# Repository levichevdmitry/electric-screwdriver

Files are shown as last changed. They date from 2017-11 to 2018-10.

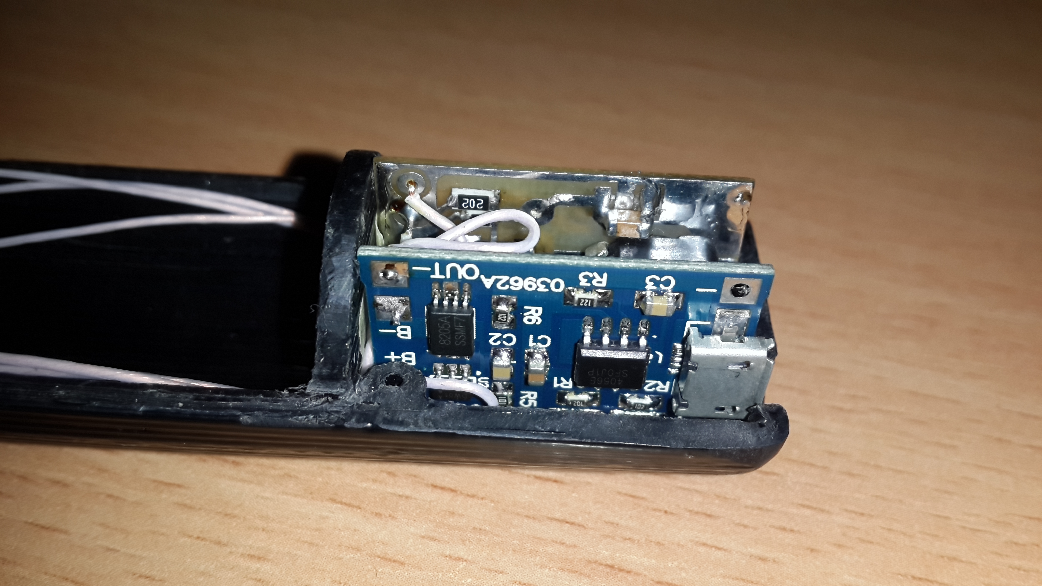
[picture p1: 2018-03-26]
foto/20171118_213815.jpg

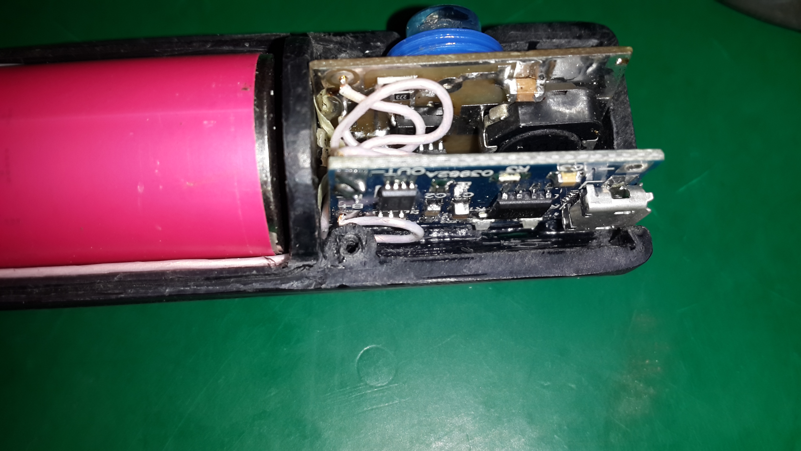
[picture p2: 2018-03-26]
foto/20180302_205503.jpg

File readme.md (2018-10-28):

Электроотвертка
-------------------------------
**Структура проекта**
- src - папка содержит исходные коды и прошивку для контроллера отвертки
- hardware - папка содержит файлы схем и печатных плат
- models - папка содержить модели корпуса и кнопок
- foto - папка содержит фото готового устройства и  этапов сборки

**Инструкция по сборке**

Смотрите статью на habr.ru
https://habr.com/post/411203/

Модели для печати лежат вот тут https://www.thingiverse.com/thing:2746308

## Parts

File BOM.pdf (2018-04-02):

Перечень элементов для сборки электроотвертки

№ | Наименование | Фото | Количество
Элементы механики

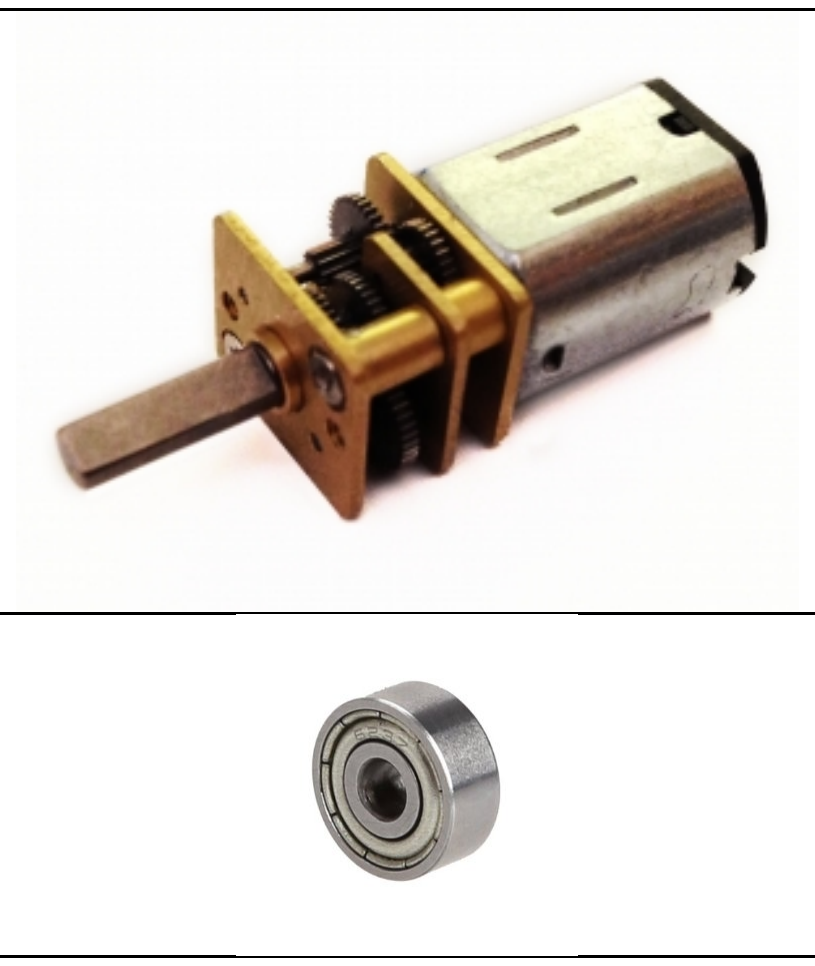
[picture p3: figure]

1. Мотор c редуктором 6В 250 об/мин | ZGRM12FT20-250 | 1
2. | Подшипник закрытый 623zz | 1
3. Муфта соединительная латунная, | внутренний диаметр 3 мм. | 1
4. | Винт стопорный 4мм х М3 | 2
5. Корпус пластиковый из 2 частей + | толкатели кнопок. Материал ABS. 3D печать. Масса используемого филамента примерно 40 г. | 1

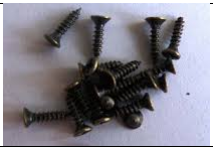
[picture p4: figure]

6. | Саморезы для сборки корпуса 2.5х6 мм | 6
7. Полоска латуни 5х15мм толщиной 0.5 мм | для контактов аккумулятора. | 2
8. | Удлинитель из набора с битами 4 мм | 1

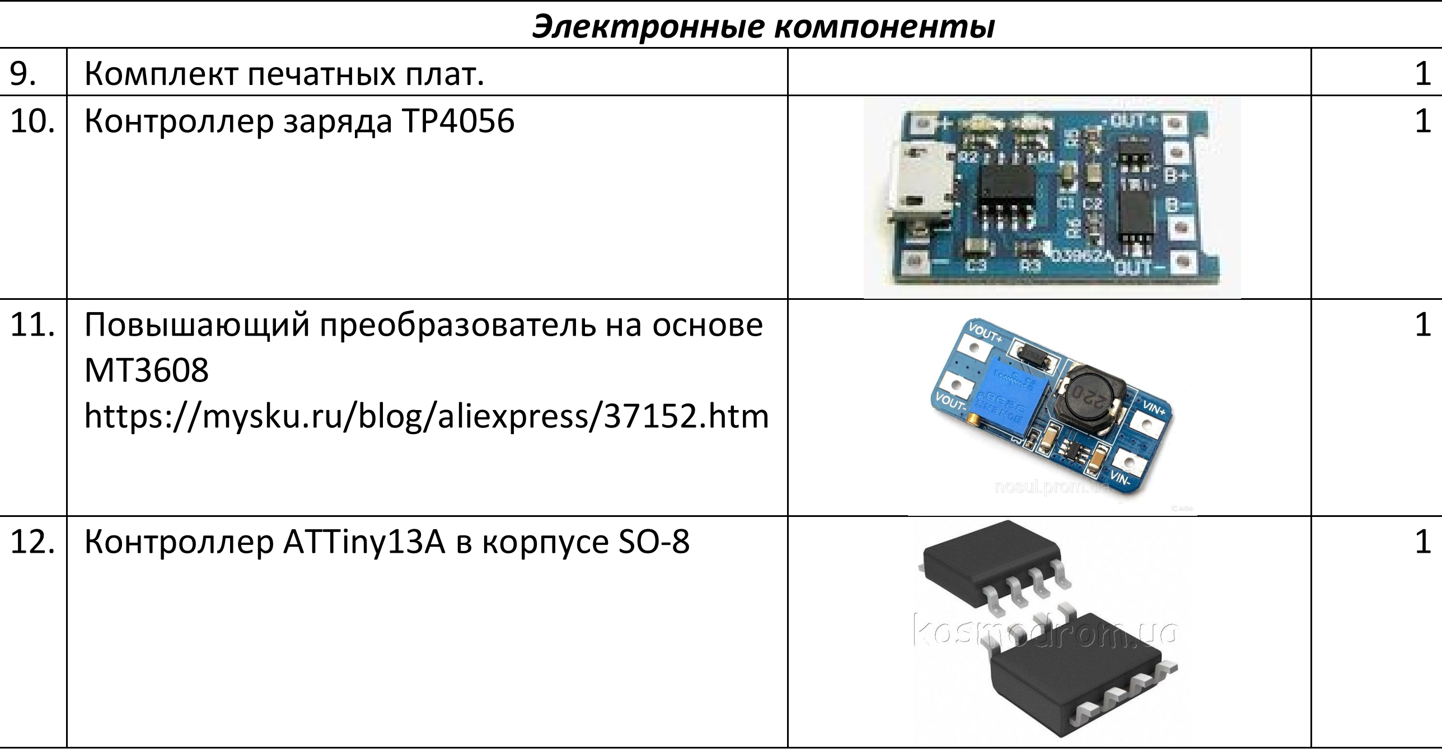
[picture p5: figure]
Электронные компоненты; Комплект печатных плат.; Контроллер заряда TP4056

11. Повышающий преобразователь на основе | MT3608 https://mysku.ru/blog/aliexpress/37152.htm | 1
12. | Контроллер ATTiny13A в корпусе SO-8 | 1

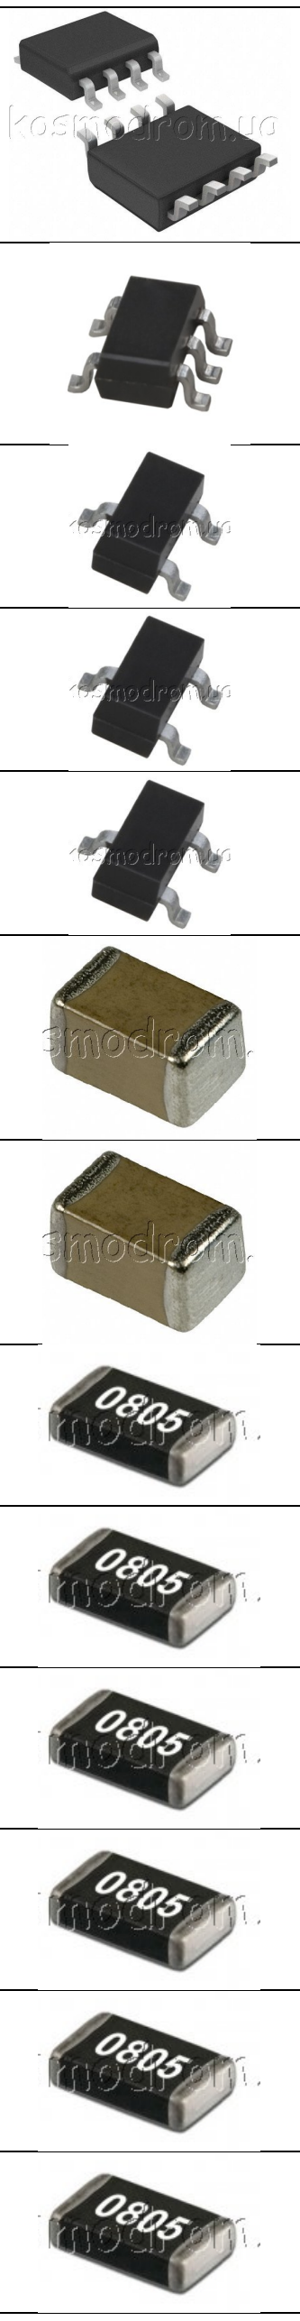
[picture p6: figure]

13. | Драйвер MX612 | 1
14. Стабилизатор 3.0В LP2981-30 в корпусе | SOT-23-5 | 1
15. | Транзистор BC817 | 2
16. | Транзистор BC857 | 1
17. | Транзистор IRLML6402 P-chanel | 1
18. | 100n 0805 | 7
19. | 1u 0805 | 1
20. | 100k 0805 | 2
21. | 27k 0805 | 1
22. | 20k 0805 | 3
23. | 10k 0805 | 6
24. | 4.7k 0805 | 2
25. | 2.7k 0805 | 1

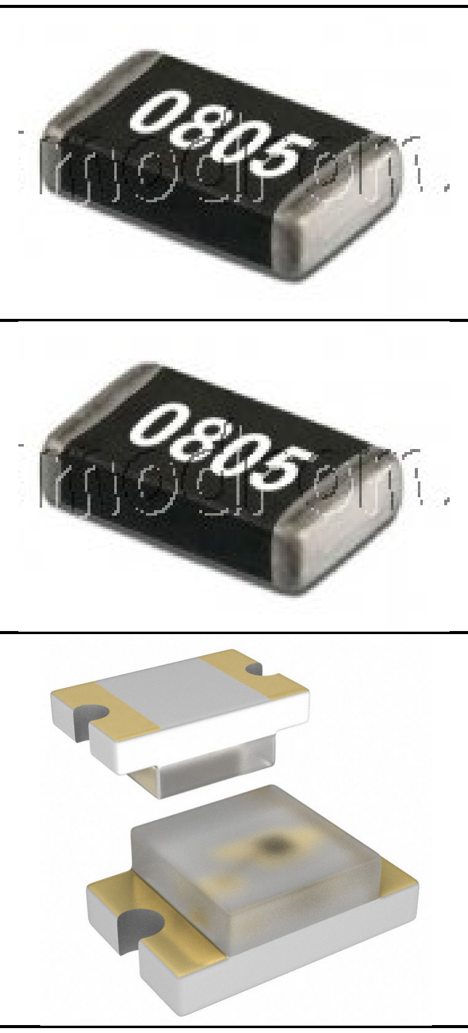
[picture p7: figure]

26. | 2k 0805 | 1
27. | 220 Om 0805 | 1
28. | Led Red 0805 | 1
29. | Провод МГТФ 0.35 мм | 0.5 м

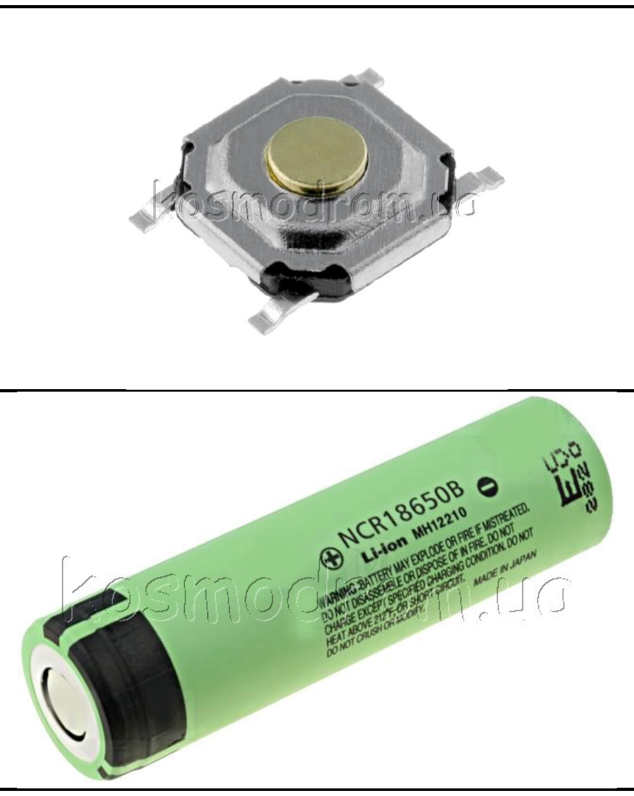
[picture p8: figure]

30. Кнопка тактовая | TACTB-64K-F | 4
31. | Аккумулятор типоразмера 18650 | 1

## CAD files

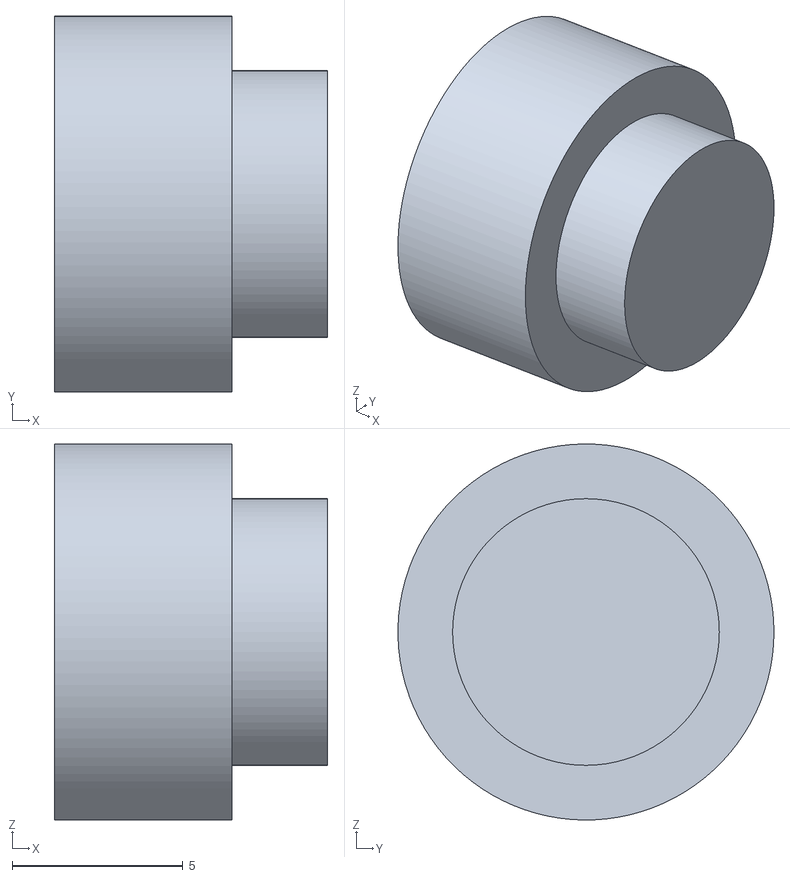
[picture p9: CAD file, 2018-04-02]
models/pwr_btn.stl
8.00 x 11.0 x 11.0

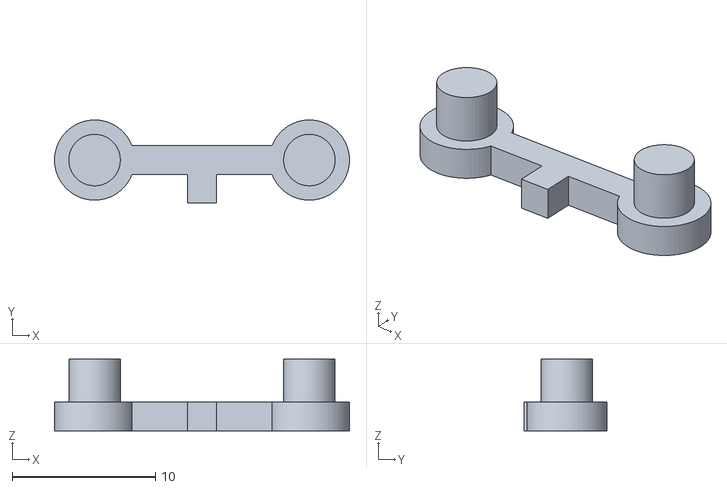
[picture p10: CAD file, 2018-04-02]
models/fwd_rev_btns.stl
20.6 x 5.80 x 5.00

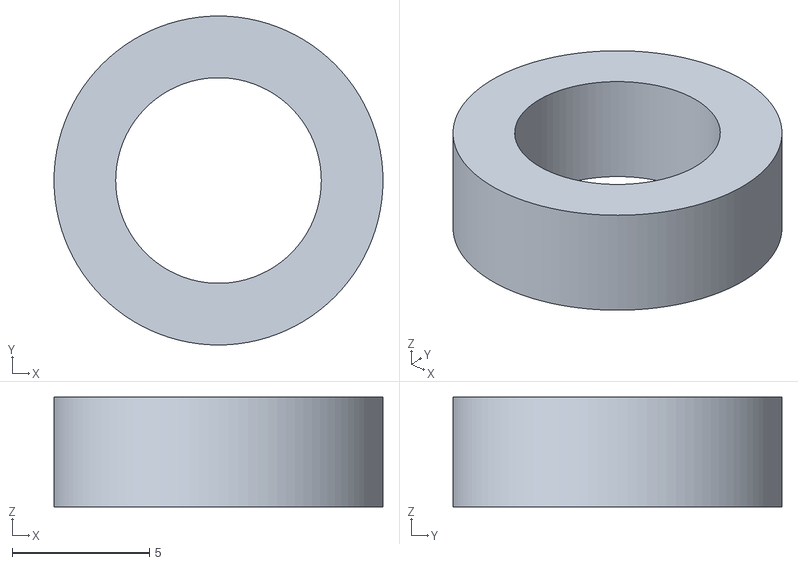
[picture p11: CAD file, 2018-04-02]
models/pwr_btn_ring.stl
12.0 x 12.0 x 4.00

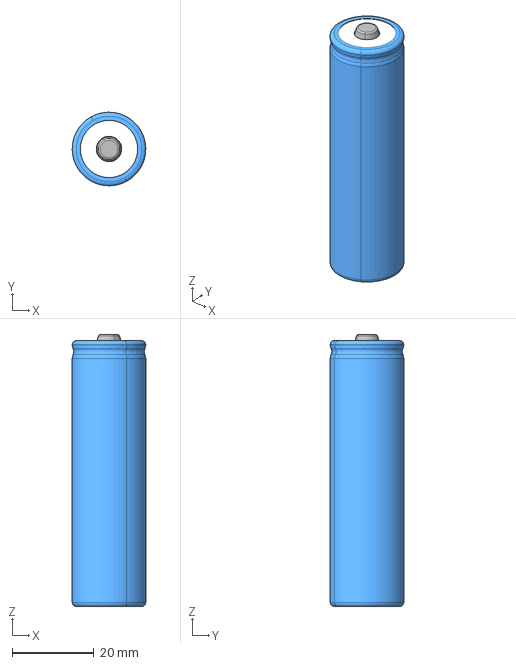
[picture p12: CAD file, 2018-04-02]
models/Battery 18650.igs
18.0 x 18.0 x 66.5 mm

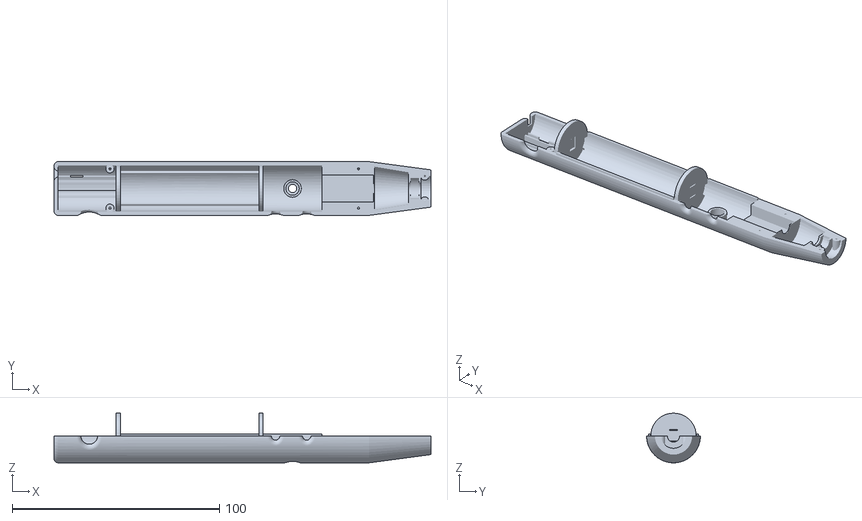
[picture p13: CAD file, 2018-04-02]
models/korpus_1.stl
182.0 x 26.0 x 24.0

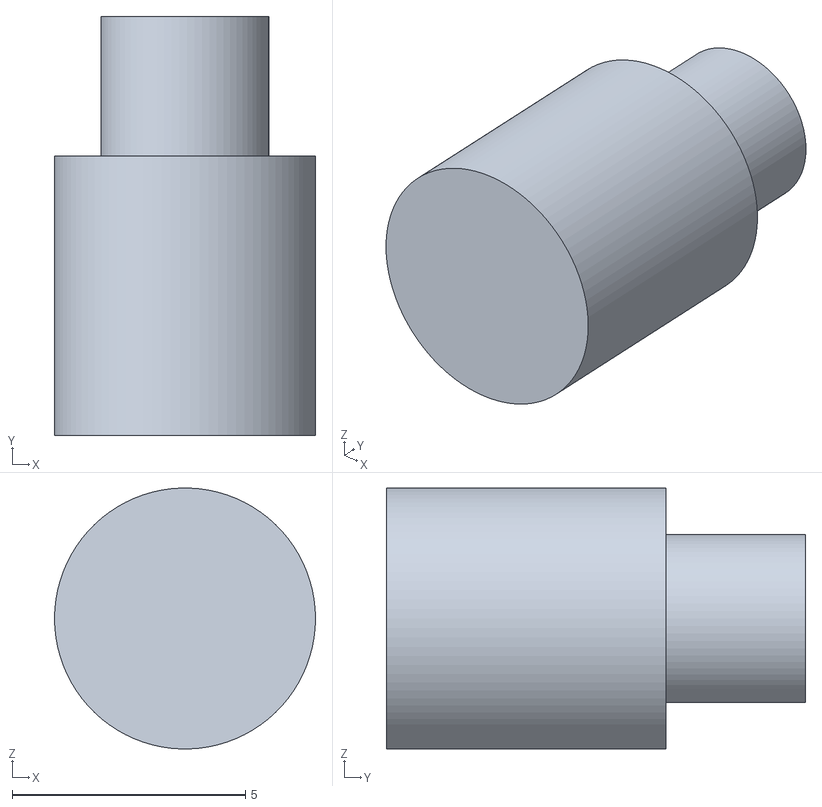
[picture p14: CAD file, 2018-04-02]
models/btn.stl
5.60 x 9.00 x 5.60

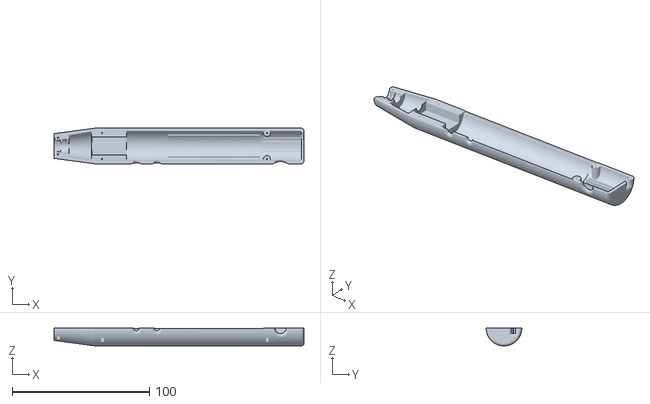
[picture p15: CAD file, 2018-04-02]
models/korpus_2.stl
182.0 x 26.0 x 13.0

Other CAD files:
models/623zz/OldVersions/roulement_623-2z_0.0001.iam
models/623zz/OldVersions/roulement_623-2z_0_01.0001.ipt
models/623zz/OldVersions/roulement_623-2z_0_02.0001.ipt
models/623zz/OldVersions/roulement_623-2z_0_03.0001.ipt
models/623zz/OldVersions/roulement_623-2z_0_04.0001.ipt
models/623zz/OldVersions/roulement_623-2z_0_05.0001.ipt
models/623zz/roulement_623-2z_0.iam
models/623zz/roulement_623-2z_0_01.ipt
models/623zz/roulement_623-2z_0_02.ipt
models/623zz/roulement_623-2z_0_03.ipt
models/623zz/roulement_623-2z_0_04.ipt
models/623zz/roulement_623-2z_0_05.ipt
models/Bateria 18650.ipt
models/Battery 18650.ipt
models/OldVersions/Vtulka.0001.ipt
models/OldVersions/btn.0002.ipt
models/OldVersions/fwd_rev_btns.0002.ipt
models/OldVersions/korpus_1.0021.ipt
models/OldVersions/korpus_2.0006.ipt
models/OldVersions/pwr_btn.0002.ipt
models/OldVersions/Сборка.0015.iam
models/TP4056.ipt
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

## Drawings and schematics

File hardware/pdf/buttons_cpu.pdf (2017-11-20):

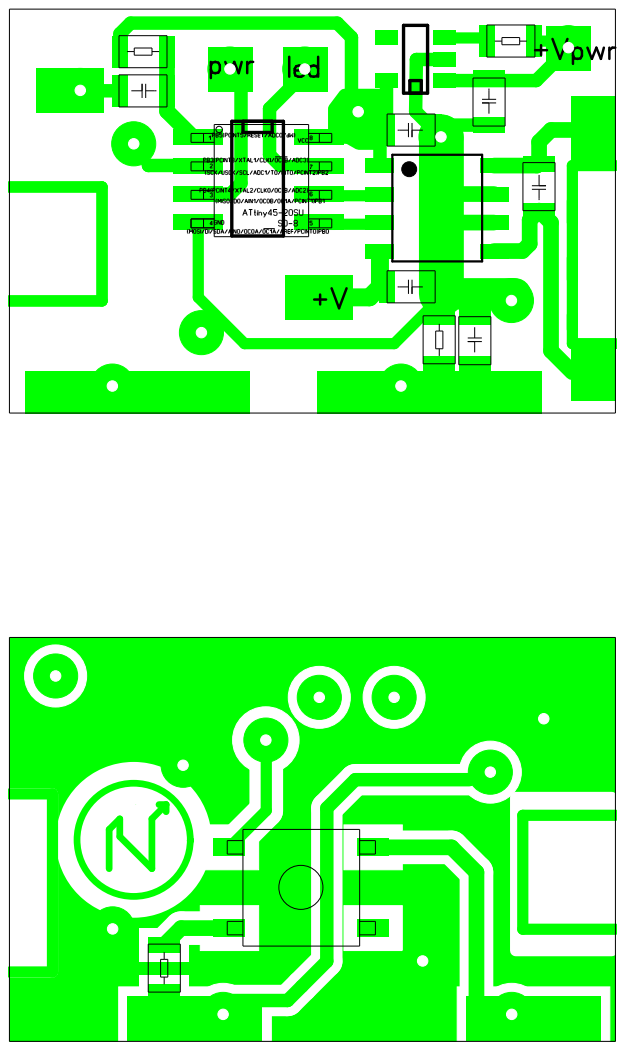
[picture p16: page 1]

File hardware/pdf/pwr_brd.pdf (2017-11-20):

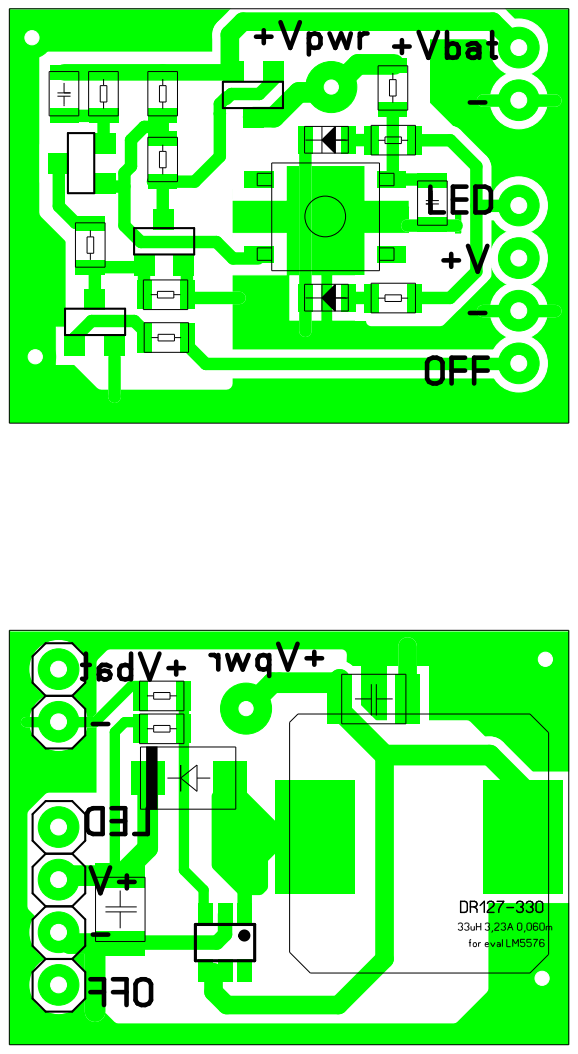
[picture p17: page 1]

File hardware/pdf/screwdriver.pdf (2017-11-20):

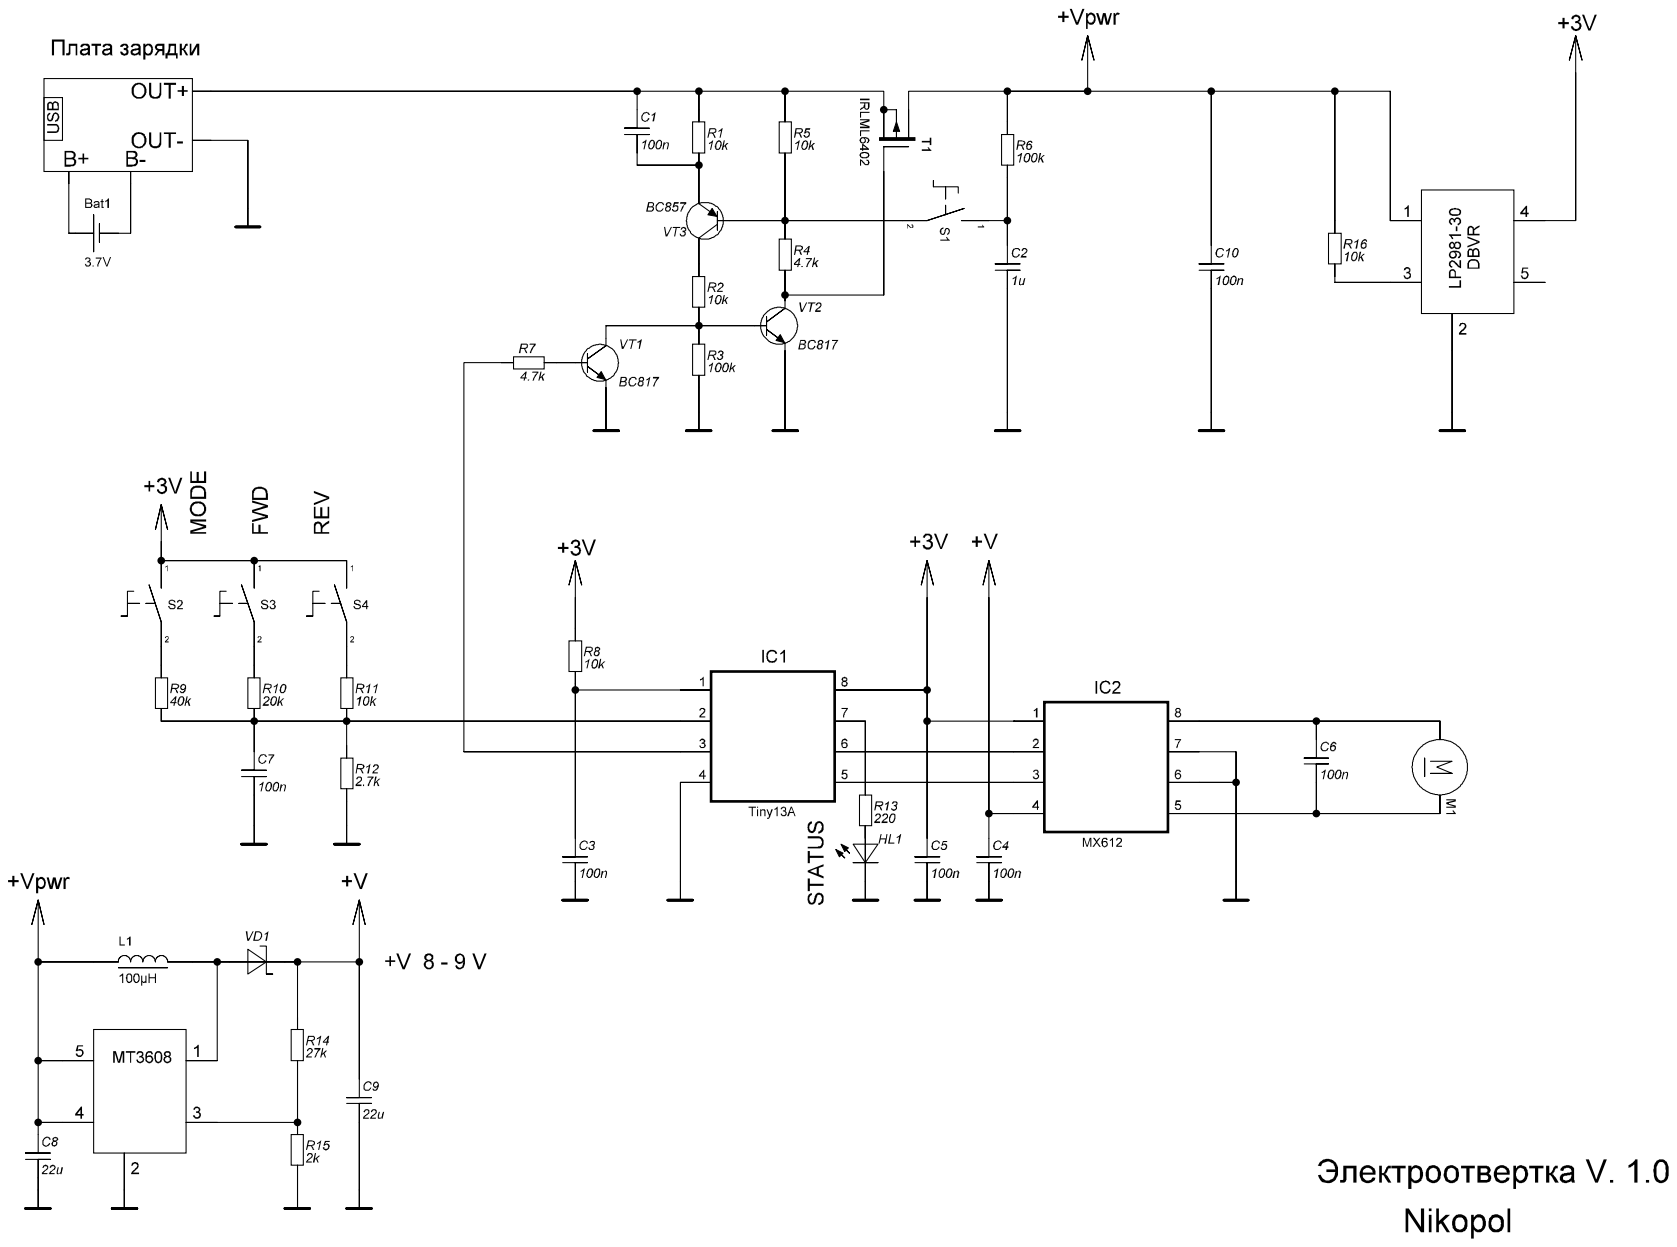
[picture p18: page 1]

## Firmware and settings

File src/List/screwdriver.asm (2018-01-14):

;CodeVisionAVR C Compiler V2.05.3 Standard
;(C) Copyright 1998-2011 Pavel Haiduc, HP InfoTech s.r.l.
;http://www.hpinfotech.com

;Chip type                : ATtiny13A
;Program type             : Application
;Clock frequency          : 9,600000 MHz
;Memory model             : Tiny
;Optimize for             : Size
;(s)printf features       : int, width
;(s)scanf features        : int, width
;External RAM size        : 0
;Data Stack size          : 16 byte(s)
;Heap size                : 0 byte(s)
;Promote 'char' to 'int'  : Yes
;'char' is unsigned       : Yes
;8 bit enums              : Yes
;Global 'const' stored in FLASH     : No
;Enhanced function parameter passing: Yes
;Smart register allocation          : Off
;Automatic register allocation      : On

	#pragma AVRPART ADMIN PART_NAME ATtiny13A
	#pragma AVRPART MEMORY PROG_FLASH 1024
	#pragma AVRPART MEMORY EEPROM 64
	#pragma AVRPART MEMORY INT_SRAM SIZE 159
	#pragma AVRPART MEMORY INT_SRAM START_ADDR 0x60

	.LISTMAC
	.EQU EERE=0x0
	.EQU EEWE=0x1
	.EQU EEMWE=0x2
	.EQU EECR=0x1C
	.EQU EEDR=0x1D
	.EQU EEARL=0x1E

	.EQU WDTCR=0x21
	.EQU MCUSR=0x34
	.EQU MCUCR=0x35
	.EQU SPL=0x3D
	.EQU SREG=0x3F

	.DEF R0X0=R0
	.DEF R0X1=R1
	.DEF R0X2=R2
	.DEF R0X3=R3
	.DEF R0X4=R4
	.DEF R0X5=R5
	.DEF R0X6=R6
	.DEF R0X7=R7
	.DEF R0X8=R8
	.DEF R0X9=R9
	.DEF R0XA=R10
	.DEF R0XB=R11
	.DEF R0XC=R12
	.DEF R0XD=R13
	.DEF R0XE=R14
	.DEF R0XF=R15
	.DEF R0X10=R16
	.DEF R0X11=R17
	.DEF R0X12=R18
	.DEF R0X13=R19
	.DEF R0X14=R20
	.DEF R0X15=R21
	.DEF R0X16=R22
	.DEF R0X17=R23
	.DEF R0X18=R24
	.DEF R0X19=R25
	.DEF R0X1A=R26
	.DEF R0X1B=R27
	.DEF R0X1C=R28
	.DEF R0X1D=R29
	.DEF R0X1E=R30
	.DEF R0X1F=R31

	.EQU __SRAM_START=0x0060
	.EQU __SRAM_END=0x009F
	.EQU __DSTACK_SIZE=0x0010
	.EQU __HEAP_SIZE=0x0000
	.EQU __CLEAR_SRAM_SIZE=__SRAM_END-__SRAM_START+1

	.MACRO __CPD1N
	CPI  R30,LOW(@0)
	LDI  R26,HIGH(@0)
	CPC  R31,R26
	LDI  R26,BYTE3(@0)
	CPC  R22,R26
	LDI  R26,BYTE4(@0)
	CPC  R23,R26
	.ENDM

	.MACRO __CPD2N
	CPI  R26,LOW(@0)
	LDI  R30,HIGH(@0)
	CPC  R27,R30
	LDI  R30,BYTE3(@0)
	CPC  R24,R30
	LDI  R30,BYTE4(@0)
	CPC  R25,R30
	.ENDM

	.MACRO __CPWRR
	CP   R@0,R@2
	CPC  R@1,R@3
	.ENDM

	.MACRO __CPWRN
	CPI  R@0,LOW(@2)
	LDI  R30,HIGH(@2)
	CPC  R@1,R30
	.ENDM

	.MACRO __ADDB1MN
	SUBI R30,LOW(-@0-(@1))
	.ENDM

	.MACRO __ADDB2MN
	SUBI R26,LOW(-@0-(@1))
	.ENDM

	.MACRO __ADDW1MN
	SUBI R30,LOW(-@0-(@1))
	SBCI R31,HIGH(-@0-(@1))
	.ENDM

	.MACRO __ADDW2MN
	SUBI R26,LOW(-@0-(@1))
	SBCI R27,HIGH(-@0-(@1))
	.ENDM

	.MACRO __ADDW1FN
	SUBI R30,LOW(-2*@0-(@1))
	SBCI R31,HIGH(-2*@0-(@1))
	.ENDM

	.MACRO __ADDD1FN
	SUBI R30,LOW(-2*@0-(@1))
	SBCI R31,HIGH(-2*@0-(@1))
	SBCI R22,BYTE3(-2*@0-(@1))
	.ENDM

	.MACRO __ADDD1N
	SUBI R30,LOW(-@0)
	SBCI R31,HIGH(-@0)
	SBCI R22,BYTE3(-@0)
	SBCI R23,BYTE4(-@0)
	.ENDM

	.MACRO __ADDD2N
	SUBI R26,LOW(-@0)
	SBCI R27,HIGH(-@0)
	SBCI R24,BYTE3(-@0)
	SBCI R25,BYTE4(-@0)
	.ENDM

	.MACRO __SUBD1N
	SUBI R30,LOW(@0)
	SBCI R31,HIGH(@0)
	SBCI R22,BYTE3(@0)
	SBCI R23,BYTE4(@0)
	.ENDM

	.MACRO __SUBD2N
	SUBI R26,LOW(@0)
	SBCI R27,HIGH(@0)
	SBCI R24,BYTE3(@0)
	SBCI R25,BYTE4(@0)
	.ENDM

	.MACRO __ANDBMNN
	LDS  R30,@0+(@1)
	ANDI R30,LOW(@2)
	STS  @0+(@1),R30
	.ENDM

	.MACRO __ANDWMNN
	LDS  R30,@0+(@1)
	ANDI R30,LOW(@2)
	STS  @0+(@1),R30
	LDS  R30,@0+(@1)+1
	ANDI R30,HIGH(@2)
	STS  @0+(@1)+1,R30
	.ENDM

	.MACRO __ANDD1N
	ANDI R30,LOW(@0)
	ANDI R31,HIGH(@0)
	ANDI R22,BYTE3(@0)
	ANDI R23,BYTE4(@0)
	.ENDM

	.MACRO __ANDD2N
	ANDI R26,LOW(@0)
	ANDI R27,HIGH(@0)
	ANDI R24,BYTE3(@0)
	ANDI R25,BYTE4(@0)
	.ENDM

	.MACRO __ORBMNN
	LDS  R30,@0+(@1)
	ORI  R30,LOW(@2)
	STS  @0+(@1),R30
	.ENDM

	.MACRO __ORWMNN
	LDS  R30,@0+(@1)
	ORI  R30,LOW(@2)
	STS  @0+(@1),R30
	LDS  R30,@0+(@1)+1
	ORI  R30,HIGH(@2)
	STS  @0+(@1)+1,R30
	.ENDM

	.MACRO __ORD1N
	ORI  R30,LOW(@0)
	ORI  R31,HIGH(@0)
	ORI  R22,BYTE3(@0)
	ORI  R23,BYTE4(@0)
	.ENDM

	.MACRO __ORD2N
	ORI  R26,LOW(@0)
	ORI  R27,HIGH(@0)
	ORI  R24,BYTE3(@0)
	ORI  R25,BYTE4(@0)
	.ENDM

	.MACRO __DELAY_USB
	LDI  R24,LOW(@0)
__DELAY_USB_LOOP:
	DEC  R24
	BRNE __DELAY_USB_LOOP
	.ENDM

	.MACRO __DELAY_USW
	LDI  R24,LOW(@0)
	LDI  R25,HIGH(@0)
__DELAY_USW_LOOP:
	SBIW R24,1
	BRNE __DELAY_USW_LOOP
	.ENDM

	.MACRO __GETD1S
	LDD  R30,Y+@0
	LDD  R31,Y+@0+1
	LDD  R22,Y+@0+2
	LDD  R23,Y+@0+3
	.ENDM

	.MACRO __GETD2S
	LDD  R26,Y+@0
	LDD  R27,Y+@0+1
	LDD  R24,Y+@0+2
	LDD  R25,Y+@0+3
	.ENDM

	.MACRO __PUTD1S
	STD  Y+@0,R30
	STD  Y+@0+1,R31
	STD  Y+@0+2,R22
	STD  Y+@0+3,R23
	.ENDM

	.MACRO __PUTD2S
	STD  Y+@0,R26
	STD  Y+@0+1,R27
	STD  Y+@0+2,R24
	STD  Y+@0+3,R25
	.ENDM

	.MACRO __PUTDZ2
	STD  Z+@0,R26
	STD  Z+@0+1,R27
	STD  Z+@0+2,R24
	STD  Z+@0+3,R25
	.ENDM

	.MACRO __CLRD1S
	STD  Y+@0,R30
	STD  Y+@0+1,R30
	STD  Y+@0+2,R30
	STD  Y+@0+3,R30
	.ENDM

	.MACRO __POINTB1MN
	LDI  R30,LOW(@0+(@1))
	.ENDM

	.MACRO __POINTW1MN
	LDI  R30,LOW(@0+(@1))
	LDI  R31,HIGH(@0+(@1))
	.ENDM

	.MACRO __POINTD1M
	LDI  R30,LOW(@0)
	LDI  R31,HIGH(@0)
	LDI  R22,BYTE3(@0)
	LDI  R23,BYTE4(@0)
	.ENDM

	.MACRO __POINTW1FN
	LDI  R30,LOW(2*@0+(@1))
	LDI  R31,HIGH(2*@0+(@1))
	.ENDM

	.MACRO __POINTD1FN
	LDI  R30,LOW(2*@0+(@1))
	LDI  R31,HIGH(2*@0+(@1))
	LDI  R22,BYTE3(2*@0+(@1))
	LDI  R23,BYTE4(2*@0+(@1))
	.ENDM

	.MACRO __POINTB2MN
	LDI  R26,LOW(@0+(@1))
	.ENDM

	.MACRO __POINTW2MN
	LDI  R26,LOW(@0+(@1))
	LDI  R27,HIGH(@0+(@1))
	.ENDM

	.MACRO __POINTW2FN
	LDI  R26,LOW(2*@0+(@1))
	LDI  R27,HIGH(2*@0+(@1))
	.ENDM

	.MACRO __POINTD2FN
	LDI  R26,LOW(2*@0+(@1))
	LDI  R27,HIGH(2*@0+(@1))
	LDI  R24,BYTE3(2*@0+(@1))
	LDI  R25,BYTE4(2*@0+(@1))
	.ENDM

	.MACRO __POINTBRM
	LDI  R@0,LOW(@1)
	.ENDM

	.MACRO __POINTWRM
	LDI  R@0,LOW(@2)
	LDI  R@1,HIGH(@2)
	.ENDM

	.MACRO __POINTBRMN
	LDI  R@0,LOW(@1+(@2))
	.ENDM

	.MACRO __POINTWRMN
	LDI  R@0,LOW(@2+(@3))
	LDI  R@1,HIGH(@2+(@3))
	.ENDM

	.MACRO __POINTWRFN
	LDI  R@0,LOW(@2*2+(@3))
	LDI  R@1,HIGH(@2*2+(@3))
	.ENDM

	.MACRO __GETD1N
	LDI  R30,LOW(@0)
	LDI  R31,HIGH(@0)
	LDI  R22,BYTE3(@0)
	LDI  R23,BYTE4(@0)
	.ENDM

	.MACRO __GETD2N
	LDI  R26,LOW(@0)
	LDI  R27,HIGH(@0)
	LDI  R24,BYTE3(@0)
	LDI  R25,BYTE4(@0)
	.ENDM

	.MACRO __GETB1MN
	LDS  R30,@0+(@1)
	.ENDM

	.MACRO __GETB1HMN
	LDS  R31,@0+(@1)
	.ENDM

	.MACRO __GETW1MN
	LDS  R30,@0+(@1)
	LDS  R31,@0+(@1)+1
	.ENDM

	.MACRO __GETD1MN
	LDS  R30,@0+(@1)
	LDS  R31,@0+(@1)+1
	LDS  R22,@0+(@1)+2
	LDS  R23,@0+(@1)+3
	.ENDM

	.MACRO __GETBRMN
	LDS  R@0,@1+(@2)
	.ENDM

	.MACRO __GETWRMN
	LDS  R@0,@2+(@3)
	LDS  R@1,@2+(@3)+1
	.ENDM

	.MACRO __GETWRZ
	LDD  R@0,Z+@2
	LDD  R@1,Z+@2+1
	.ENDM

	.MACRO __GETD2Z
	LDD  R26,Z+@0
	LDD  R27,Z+@0+1
	LDD  R24,Z+@0+2
	LDD  R25,Z+@0+3
	.ENDM

	.MACRO __GETB2MN
	LDS  R26,@0+(@1)
	.ENDM

	.MACRO __GETW2MN
	LDS  R26,@0+(@1)
	LDS  R27,@0+(@1)+1
	.ENDM

	.MACRO __GETD2MN
	LDS  R26,@0+(@1)
	LDS  R27,@0+(@1)+1
	LDS  R24,@0+(@1)+2
	LDS  R25,@0+(@1)+3
	.ENDM

	.MACRO __PUTB1MN
	STS  @0+(@1),R30
	.ENDM

	.MACRO __PUTW1MN
	STS  @0+(@1),R30
	STS  @0+(@1)+1,R31
	.ENDM

	.MACRO __PUTD1MN
	STS  @0+(@1),R30
	STS  @0+(@1)+1,R31
	STS  @0+(@1)+2,R22
	STS  @0+(@1)+3,R23
	.ENDM

	.MACRO __PUTB1EN
	LDI  R26,LOW(@0+(@1))
	LDI  R27,HIGH(@0+(@1))
	RCALL __EEPROMWRB
	.ENDM

	.MACRO __PUTW1EN
	LDI  R26,LOW(@0+(@1))
	LDI  R27,HIGH(@0+(@1))
	RCALL __EEPROMWRW
	.ENDM

	.MACRO __PUTD1EN
	LDI  R26,LOW(@0+(@1))
	LDI  R27,HIGH(@0+(@1))
	RCALL __EEPROMWRD
	.ENDM

	.MACRO __PUTBR0MN
	STS  @0+(@1),R0
	.ENDM

	.MACRO __PUTBMRN
	STS  @0+(@1),R@2
	.ENDM

	.MACRO __PUTWMRN
	STS  @0+(@1),R@2
	STS  @0+(@1)+1,R@3
	.ENDM

	.MACRO __PUTBZR
	STD  Z+@1,R@0
	.ENDM

	.MACRO __PUTWZR
	STD  Z+@2,R@0
	STD  Z+@2+1,R@1
	.ENDM

	.MACRO __GETW1R
	MOV  R30,R@0
	MOV  R31,R@1
	.ENDM

	.MACRO __GETW2R
	MOV  R26,R@0
	MOV  R27,R@1
	.ENDM

	.MACRO __GETWRN
	LDI  R@0,LOW(@2)
	LDI  R@1,HIGH(@2)
	.ENDM

	.MACRO __PUTW1R
	MOV  R@0,R30
	MOV  R@1,R31
	.ENDM

	.MACRO __PUTW2R
	MOV  R@0,R26
	MOV  R@1,R27
	.ENDM

	.MACRO __ADDWRN
	SUBI R@0,LOW(-@2)
	SBCI R@1,HIGH(-@2)
	.ENDM

	.MACRO __ADDWRR
	ADD  R@0,R@2
	ADC  R@1,R@3
	.ENDM

	.MACRO __SUBWRN
	SUBI R@0,LOW(@2)
	SBCI R@1,HIGH(@2)
	.ENDM

	.MACRO __SUBWRR
	SUB  R@0,R@2
	SBC  R@1,R@3
	.ENDM

	.MACRO __ANDWRN
	ANDI R@0,LOW(@2)
	ANDI R@1,HIGH(@2)
	.ENDM

	.MACRO __ANDWRR
	AND  R@0,R@2
	AND  R@1,R@3
	.ENDM

	.MACRO __ORWRN
	ORI  R@0,LOW(@2)
	ORI  R@1,HIGH(@2)
	.ENDM

	.MACRO __ORWRR
	OR   R@0,R@2
	OR   R@1,R@3
	.ENDM

	.MACRO __EORWRR
	EOR  R@0,R@2
	EOR  R@1,R@3
	.ENDM

	.MACRO __GETWRS
	LDD  R@0,Y+@2
	LDD  R@1,Y+@2+1
	.ENDM

	.MACRO __PUTBSR
	STD  Y+@1,R@0
	.ENDM

	.MACRO __PUTWSR
	STD  Y+@2,R@0
	STD  Y+@2+1,R@1
	.ENDM

	.MACRO __MOVEWRR
	MOV  R@0,R@2
	MOV  R@1,R@3
	.ENDM

	.MACRO __INWR
	IN   R@0,@2
	IN   R@1,@2+1
	.ENDM

	.MACRO __OUTWR
	OUT  @2+1,R@1
	OUT  @2,R@0
	.ENDM

	.MACRO __CALL1MN
	LDS  R30,@0+(@1)
	LDS  R31,@0+(@1)+1
	ICALL
	.ENDM

	.MACRO __CALL1FN
	LDI  R30,LOW(2*@0+(@1))
	LDI  R31,HIGH(2*@0+(@1))
	RCALL __GETW1PF
	ICALL
	.ENDM

	.MACRO __CALL2EN
	LDI  R26,LOW(@0+(@1))
	LDI  R27,HIGH(@0+(@1))
	RCALL __EEPROMRDW
	ICALL
	.ENDM

	.MACRO __GETW1STACK
	IN   R26,SPL
	IN   R27,SPH
	ADIW R26,@0+1
	LD   R30,X+
	LD   R31,X
	.ENDM

	.MACRO __GETD1STACK
	IN   R26,SPL
	IN   R27,SPH
	ADIW R26,@0+1
	LD   R30,X+
	LD   R31,X+
	LD   R22,X
	.ENDM

	.MACRO __NBST
	BST  R@0,@1
	IN   R30,SREG
	LDI  R31,0x40
	EOR  R30,R31
	OUT  SREG,R30
	.ENDM


	.MACRO __PUTB1SN
	LDD  R26,Y+@0
	SUBI R26,-@1
	ST   X,R30
	.ENDM

	.MACRO __PUTW1SN
	LDD  R26,Y+@0
	SUBI R26,-@1
	ST   X+,R30
	ST   X,R31
	.ENDM

	.MACRO __PUTD1SN
	LDD  R26,Y+@0
	SUBI R26,-@1
	RCALL __PUTDP1
	.ENDM

	.MACRO __PUTB1SNS
	LDD  R26,Y+@0
	SUBI R26,-@1
	ST   X,R30
	.ENDM

	.MACRO __PUTW1SNS
	LDD  R26,Y+@0
	SUBI R26,-@1
	ST   X+,R30
	ST   X,R31
	.ENDM

	.MACRO __PUTD1SNS
	LDD  R26,Y+@0
	SUBI R26,-@1
	RCALL __PUTDP1
	.ENDM

	.MACRO __PUTB1RN
	MOV  R26,R@0
	SUBI R26,-@1
	ST   X,R30
	.ENDM

	.MACRO __PUTW1RN
	MOV  R26,R@0
	SUBI R26,-@1
	ST   X+,R30
	ST   X,R31
	.ENDM

	.MACRO __PUTD1RN
	MOV  R26,R@0
	SUBI R26,-@1
	RCALL __PUTDP1
	.ENDM

	.MACRO __PUTB1RNS
	MOV  R26,R@0
	SUBI R26,-@1
	ST   X,R30
	.ENDM

	.MACRO __PUTW1RNS
	MOV  R26,R@0
	SUBI R26,-@1
	ST   X+,R30
	ST   X,R31
	.ENDM

	.MACRO __PUTD1RNS
	MOV  R26,R@0
	SUBI R26,-@1
	RCALL __PUTDP1
	.ENDM

	.MACRO __PUTB1PMN
	LDS  R26,@0
	SUBI R26,-@1
	ST   X,R30
	.ENDM

	.MACRO __PUTW1PMN
	LDS  R26,@0
	SUBI R26,-@1
	ST   X+,R30
	ST   X,R31
	.ENDM

	.MACRO __PUTD1PMN
	LDS  R26,@0
	SUBI R26,-@1
	RCALL __PUTDP1
	.ENDM

	.MACRO __PUTB1PMNS
	LDS  R26,@0
	SUBI R26,-@1
	ST   X,R30
	.ENDM

	.MACRO __PUTW1PMNS
	LDS  R26,@0
	SUBI R26,-@1
	ST   X+,R30
	ST   X,R31
	.ENDM

	.MACRO __PUTD1PMNS
	LDS  R26,@0
	SUBI R26,-@1
	RCALL __PUTDP1
	.ENDM

	.MACRO __GETB1SX
	MOV  R30,R28
	MOV  R31,R29
	SUBI R30,LOW(-@0)
	SBCI R31,HIGH(-@0)
	LD   R30,Z
	.ENDM

	.MACRO __GETB1HSX
	MOV  R30,R28
	MOV  R31,R29
	SUBI R30,LOW(-@0)
	SBCI R31,HIGH(-@0)
	LD   R31,Z
	.ENDM

	.MACRO __GETW1SX
	MOV  R30,R28
	MOV  R31,R29
	SUBI R30,LOW(-@0)
	SBCI R31,HIGH(-@0)
	LD   R0,Z+
	LD   R31,Z
	MOV  R30,R0
	.ENDM

	.MACRO __GETD1SX
	MOV  R30,R28
	MOV  R31,R29
	SUBI R30,LOW(-@0)
	SBCI R31,HIGH(-@0)
	LD   R0,Z+
	LD   R1,Z+
	LD   R22,Z+
	LD   R23,Z
	MOV  R30,R0
	MOV  R31,R1
	.ENDM

	.MACRO __GETB2SX
	MOV  R26,R28
	MOV  R27,R29
	SUBI R26,LOW(-@0)
	SBCI R27,HIGH(-@0)
	LD   R26,X
	.ENDM

	.MACRO __GETW2SX
	MOV  R26,R28
	MOV  R27,R29
	SUBI R26,LOW(-@0)
	SBCI R27,HIGH(-@0)
	LD   R0,X+
	LD   R27,X
	MOV  R26,R0
	.ENDM

	.MACRO __GETD2SX
	MOV  R26,R28
	MOV  R27,R29
	SUBI R26,LOW(-@0)
	SBCI R27,HIGH(-@0)
	LD   R0,X+
	LD   R1,X+
	LD   R24,X+
	LD   R25,X
	MOV  R26,R0
	MOV  R27,R1
	.ENDM

	.MACRO __GETBRSX
	MOV  R30,R28
	MOV  R31,R29
	SUBI R30,LOW(-@1)
	SBCI R31,HIGH(-@1)
	LD   R@0,Z
	.ENDM

	.MACRO __GETWRSX
	MOV  R30,R28
	MOV  R31,R29
	SUBI R30,LOW(-@2)
	SBCI R31,HIGH(-@2)
	LD   R@0,Z+
	LD   R@1,Z
	.ENDM

	.MACRO __GETBRSX2
	MOV  R26,R28
	MOV  R27,R29
	SUBI R26,LOW(-@1)
	SBCI R27,HIGH(-@1)
	LD   R@0,X
	.ENDM

	.MACRO __GETWRSX2
	MOV  R26,R28
	MOV  R27,R29
	SUBI R26,LOW(-@2)
	SBCI R27,HIGH(-@2)
	LD   R@0,X+
	LD   R@1,X
	.ENDM

	.MACRO __LSLW8SX
	MOV  R30,R28
	MOV  R31,R29
	SUBI R30,LOW(-@0)
	SBCI R31,HIGH(-@0)
	LD   R31,Z
	CLR  R30
	.ENDM

	.MACRO __PUTB1SX
	MOV  R26,R28
	MOV  R27,R29
	SUBI R26,LOW(-@0)
	SBCI R27,HIGH(-@0)
	ST   X,R30
	.ENDM

	.MACRO __PUTW1SX
	MOV  R26,R28
	MOV  R27,R29
	SUBI R26,LOW(-@0)
	SBCI R27,HIGH(-@0)
	ST   X+,R30
	ST   X,R31
	.ENDM

	.MACRO __PUTD1SX
	MOV  R26,R28
	MOV  R27,R29
	SUBI R26,LOW(-@0)
	SBCI R27,HIGH(-@0)
	ST   X+,R30
	ST   X+,R31
	ST   X+,R22
	ST   X,R23
	.ENDM

	.MACRO __CLRW1SX
	MOV  R26,R28
	MOV  R27,R29
	SUBI R26,LOW(-@0)
	SBCI R27,HIGH(-@0)
	ST   X+,R30
	ST   X,R30
	.ENDM

	.MACRO __CLRD1SX
	MOV  R26,R28
	MOV  R27,R29
	SUBI R26,LOW(-@0)
	SBCI R27,HIGH(-@0)
	ST   X+,R30
	ST   X+,R30
	ST   X+,R30
	ST   X,R30
	.ENDM

	.MACRO __PUTB2SX
	MOV  R30,R28
	MOV  R31,R29
	SUBI R30,LOW(-@0)
	SBCI R31,HIGH(-@0)
	ST   Z,R26
	.ENDM

	.MACRO __PUTW2SX
	MOV  R30,R28
	MOV  R31,R29
	SUBI R30,LOW(-@0)
	SBCI R31,HIGH(-@0)
	ST   Z+,R26
	ST   Z,R27
	.ENDM

	.MACRO __PUTD2SX
	MOV  R30,R28
	MOV  R31,R29
	SUBI R30,LOW(-@0)
	SBCI R31,HIGH(-@0)
	ST   Z+,R26
	ST   Z+,R27
	ST   Z+,R24
	ST   Z,R25
	.ENDM

	.MACRO __PUTBSRX
	MOV  R30,R28
	MOV  R31,R29
	SUBI R30,LOW(-@1)
	SBCI R31,HIGH(-@1)
	ST   Z,R@0
	.ENDM

	.MACRO __PUTWSRX
	MOV  R30,R28
	MOV  R31,R29
	SUBI R30,LOW(-@2)
	SBCI R31,HIGH(-@2)
	ST   Z+,R@0
	ST   Z,R@1
	.ENDM

	.MACRO __PUTB1SNX
	MOV  R26,R28
	MOV  R27,R29
	SUBI R26,LOW(-@0)
	SBCI R27,HIGH(-@0)
	LD   R0,X+
	LD   R27,X
	MOV  R26,R0
	SUBI R26,LOW(-@1)
	SBCI R27,HIGH(-@1)
	ST   X,R30
	.ENDM

	.MACRO __PUTW1SNX
	MOV  R26,R28
	MOV  R27,R29
	SUBI R26,LOW(-@0)
	SBCI R27,HIGH(-@0)
	LD   R0,X+
	LD   R27,X
	MOV  R26,R0
	SUBI R26,LOW(-@1)
	SBCI R27,HIGH(-@1)
	ST   X+,R30
	ST   X,R31
	.ENDM

	.MACRO __PUTD1SNX
	MOV  R26,R28
	MOV  R27,R29
	SUBI R26,LOW(-@0)
	SBCI R27,HIGH(-@0)
	LD   R0,X+
	LD   R27,X
	MOV  R26,R0
	SUBI R26,LOW(-@1)
	SBCI R27,HIGH(-@1)
	ST   X+,R30
	ST   X+,R31
	ST   X+,R22
	ST   X,R23
	.ENDM

;NAME DEFINITIONS FOR GLOBAL VARIABLES ALLOCATED TO REGISTERS
	.DEF _mode=R4
	.DEF _btn_mode_trig=R5
	.DEF _sec=R6
	.DEF _ms=R8
	.DEF _tick=R10

	.CSEG
	.ORG 0x00

;START OF CODE MARKER
__START_OF_CODE:

;INTERRUPT VECTORS
	RJMP __RESET
	RJMP 0x00
	RJMP 0x00
	RJMP _timer0_ovf_isr
	RJMP 0x00
	RJMP 0x00
	RJMP 0x00
	RJMP 0x00
	RJMP 0x00
	RJMP _adc_isr

_0x3:
	.DB  0x0,0x3F,0x7F
_0x1C:
	.DB  0x1,0x0
_0x2000060:
	.DB  0x1
_0x2000000:
	.DB  0x2D,0x4E,0x41,0x4E,0x0,0x49,0x4E,0x46
	.DB  0x0

__GLOBAL_INI_TBL:
	.DW  0x03
	.DW  _speed
	.DW  _0x3*2

	.DW  0x02
	.DW  0x04
	.DW  _0x1C*2

	.DW  0x01
	.DW  __seed_G100
	.DW  _0x2000060*2

_0xFFFFFFFF:
	.DW  0

__RESET:
	CLI
	CLR  R30
	OUT  EECR,R30
	OUT  MCUCR,R30

;DISABLE WATCHDOG
	LDI  R31,0x18
	IN   R26,MCUSR
	CBR  R26,8
	OUT  MCUSR,R26
	OUT  WDTCR,R31
	OUT  WDTCR,R30

;CLEAR R2-R14
	LDI  R24,(14-2)+1
	LDI  R26,2
__CLEAR_REG:
	ST   X+,R30
	DEC  R24
	BRNE __CLEAR_REG

;CLEAR SRAM
	LDI  R24,__CLEAR_SRAM_SIZE
	LDI  R26,__SRAM_START
__CLEAR_SRAM:
	ST   X+,R30
	DEC  R24
	BRNE __CLEAR_SRAM

;GLOBAL VARIABLES INITIALIZATION
	LDI  R30,LOW(__GLOBAL_INI_TBL*2)
	LDI  R31,HIGH(__GLOBAL_INI_TBL*2)
__GLOBAL_INI_NEXT:
	LPM
	ADIW R30,1
	MOV  R24,R0
	LPM
	ADIW R30,1
	MOV  R25,R0
	SBIW R24,0
	BREQ __GLOBAL_INI_END
	LPM
	ADIW R30,1
	MOV  R26,R0
	LPM
	ADIW R30,1
	MOV  R27,R0
	LPM
	ADIW R30,1
	MOV  R1,R0
	LPM
	ADIW R30,1
	MOV  R22,R30
	MOV  R23,R31
	MOV  R31,R0
	MOV  R30,R1
__GLOBAL_INI_LOOP:
	LPM
	ADIW R30,1
	ST   X+,R0
	SBIW R24,1
	BRNE __GLOBAL_INI_LOOP
	MOV  R30,R22
	MOV  R31,R23
	RJMP __GLOBAL_INI_NEXT
__GLOBAL_INI_END:

;HARDWARE STACK POINTER INITIALIZATION
	LDI  R30,LOW(__SRAM_END-__HEAP_SIZE)
	OUT  SPL,R30
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
;void main(void)
; 0000 0065 {
_main:
; 0000 0066 // Declare your local variables here
; 0000 0067 
; 0000 0068 // Crystal Oscillator division factor: 1
; 0000 0069 #pragma optsize-
; 0000 006A CLKPR=0x80;
	LDI  R30,LOW(128)
	OUT  0x26,R30
; 0000 006B CLKPR=0x00;
	LDI  R30,LOW(0)
	OUT  0x26,R30
; 0000 006C #ifdef _OPTIMIZE_SIZE_
; 0000 006D #pragma optsize+
; 0000 006E #endif
; 0000 006F 
; 0000 0070 // Input/Output Ports initialization
; 0000 0071 // Port B initialization
; 0000 0072 // Func5=In Func4=Out Func3=In Func2=Out Func1=Out Func0=Out
; 0000 0073 // State5=T State4=0 State3=T State2=0 State1=0 State0=0
; 0000 0074 PORTB=0x00;
	OUT  0x18,R30
; 0000 0075 DDRB=0x17;
	LDI  R30,LOW(23)
	OUT  0x17,R30
; 0000 0076 
; 0000 0077 // Timer/Counter 0 initialization
; 0000 0078 // Clock source: System Clock
; 0000 0079 // Clock value: 1200,000 kHz
; 0000 007A // Mode: Fast PWM top=0xFF
; 0000 007B // OC0A output: Inverted PWM
; 0000 007C // OC0B output: Inverted PWM
; 0000 007D TCCR0A=0xF3;
	LDI  R30,LOW(243)
	OUT  0x2F,R30
; 0000 007E TCCR0B=0x02;
	LDI  R30,LOW(2)
	OUT  0x33,R30
; 0000 007F TCNT0=0x00;
	LDI  R30,LOW(0)
	OUT  0x32,R30
; 0000 0080 OCR0A=0x00;
	OUT  0x36,R30
; 0000 0081 OCR0B=0x00;
	OUT  0x29,R30
; 0000 0082 
; 0000 0083 // External Interrupt(s) initialization
; 0000 0084 // INT0: Off
; 0000 0085 // Interrupt on any change on pins PCINT0-5: Off
; 0000 0086 GIMSK=0x00;
	OUT  0x3B,R30
; 0000 0087 MCUCR=0x00;
	OUT  0x35,R30
; 0000 0088 
; 0000 0089 // Timer/Counter 0 Interrupt(s) initialization
; 0000 008A TIMSK0=0x02;
	LDI  R30,LOW(2)
	OUT  0x39,R30
; 0000 008B 
; 0000 008C // Analog Comparator initialization
; 0000 008D // Analog Comparator: Off
; 0000 008E ACSR=0x80;
	LDI  R30,LOW(128)
	OUT  0x8,R30
; 0000 008F ADCSRB=0x00;
	LDI  R30,LOW(0)
	OUT  0x3,R30
; 0000 0090 DIDR0=0x00;
	OUT  0x14,R30
; 0000 0091 
; 0000 0092 // ADC initialization
; 0000 0093 // ADC Clock frequency: 600,000 kHz
; 0000 0094 // ADC Bandgap Voltage Reference: On
; 0000 0095 // ADC Auto Trigger Source: Timer0 Overflow
; 0000 0096 // Digital input buffers on ADC0: On, ADC1: On, ADC2: On, ADC3: Off
; 0000 0097 DIDR0&=0x03;
	IN   R30,0x14
	ANDI R30,LOW(0x3)
	OUT  0x14,R30
; 0000 0098 DIDR0|=0x08;
	SBI  0x14,3
; 0000 0099 ADMUX=FIRST_ADC_INPUT | (ADC_VREF_TYPE & 0xff);
	LDI  R30,LOW(67)
	OUT  0x7,R30
; 0000 009A ADCSRA=0xAC;
	LDI  R30,LOW(172)
	OUT  0x6,R30
; 0000 009B ADCSRB&=0xF8;
	IN   R30,0x3
	ANDI R30,LOW(0xF8)
	OUT  0x3,R30
; 0000 009C ADCSRB|=0x04;
	SBI  0x3,2
; 0000 009D 
; 0000 009E sec = 0;
	CLR  R6
	CLR  R7
; 0000 009F ms = 0;
	CLR  R8
	CLR  R9
; 0000 00A0 tick = 0;
	CLR  R10
	CLR  R11
; 0000 00A1 // Global enable interrupts
; 0000 00A2 #asm("sei")
	sei
; 0000 00A3 
; 0000 00A4 while (1)
_0x10:
; 0000 00A5       {
; 0000 00A6         if (abs(adc_data[0] - KEY_MODE_VAL) <=  KEY_DELTA_VAL) {
	RCALL SUBOPT_0x1
	SUBI R26,LOW(605)
	SBCI R27,HIGH(605)
	RCALL _abs
	SBIW R30,51
	BRSH _0x13
; 0000 00A7             if (!btn_mode_trig) {
	TST  R5
	BRNE _0x14
; 0000 00A8                 // press "mode" key detected
; 0000 00A9                 mode ++;
	INC  R4
; 0000 00AA                 if (mode > MODE_COUNT) {
	LDI  R30,LOW(2)
	CP   R30,R4
	BRSH _0x15
; 0000 00AB                     mode = 0;
	CLR  R4
; 0000 00AC                 }
; 0000 00AD             }
_0x15:
; 0000 00AE             btn_mode_trig = 1;
_0x14:
	LDI  R30,LOW(1)
	MOV  R5,R30
; 0000 00AF         } else {
	RJMP _0x16
_0x13:
; 0000 00B0             btn_mode_trig = 0;
	CLR  R5
; 0000 00B1         }
_0x16:
; 0000 00B2 
; 0000 00B3         if (abs(adc_data[0] - KEY_FWD_VAL) <=  KEY_DELTA_VAL) {
	RCALL SUBOPT_0x1
	SUBI R26,LOW(344)
	SBCI R27,HIGH(344)
	RCALL _abs
	SBIW R30,51
	BRSH _0x17
; 0000 00B4             //STATUS_LED_OFF;
; 0000 00B5              OCR0A = speed[mode];
	LDI  R26,LOW(_speed)
	ADD  R26,R4
	LD   R30,X
	OUT  0x36,R30
; 0000 00B6             sec = 0;
	CLR  R6
	CLR  R7
; 0000 00B7         } else if (abs(adc_data[0] - KEY_REV_VAL) <=  KEY_DELTA_VAL) {
	RJMP _0x18
_0x17:
	RCALL SUBOPT_0x1
	SUBI R26,LOW(186)
	SBCI R27,HIGH(186)
	RCALL _abs
	SBIW R30,51
	BRSH _0x19
; 0000 00B8             //STATUS_LED_OFF;
; 0000 00B9             OCR0B = speed[mode];
	LDI  R26,LOW(_speed)
	ADD  R26,R4
	LD   R30,X
	OUT  0x29,R30
; 0000 00BA             sec = 0;
	CLR  R6
	CLR  R7
; 0000 00BB         } else {
	RJMP _0x1A
_0x19:
; 0000 00BC             // off all
; 0000 00BD             OCR0A=0xFF;
	LDI  R30,LOW(255)
	OUT  0x36,R30
; 0000 00BE             OCR0B=0xFF;
	OUT  0x29,R30
; 0000 00BF             //STATUS_LED_OFF;
; 0000 00C0         }
_0x1A:
_0x18:
; 0000 00C1 
; 0000 00C2       }
	RJMP _0x10
; 0000 00C3 }
_0x1B:
	RJMP _0x1B

	.CSEG
_abs:
	ST   -Y,R27
	ST   -Y,R26
    ld   r30,y+
    ld   r31,y+
    sbiw r30,0
    brpl __abs0
    com  r30
    com  r31
    adiw r30,1
__abs0:
    ret

	.DSEG

	.CSEG

	.CSEG

	.CSEG

	.CSEG

	.DSEG
_speed:
	.BYTE 0x3
_adc_data:
	.BYTE 0x2
_input_index_S0000001000:
	.BYTE 0x1
__seed_G100:
	.BYTE 0x4

	.CSEG
;OPTIMIZER ADDED SUBROUTINE, CALLED 2 TIMES, CODE SIZE REDUCTION:1 WORDS
SUBOPT_0x0:
	IN   R30,0x18
	LDI  R26,LOW(4)
	EOR  R30,R26
	OUT  0x18,R30
	RET

;OPTIMIZER ADDED SUBROUTINE, CALLED 3 TIMES, CODE SIZE REDUCTION:4 WORDS
SUBOPT_0x1:
	LDS  R26,_adc_data
	LDS  R27,_adc_data+1
	RET


	.CSEG
__DIVW21U:
	CLR  R0
	CLR  R1
	LDI  R25,16
__DIVW21U1:
	LSL  R26
	ROL  R27
	ROL  R0
	ROL  R1
	SUB  R0,R30
	SBC  R1,R31
	BRCC __DIVW21U2
	ADD  R0,R30
	ADC  R1,R31
	RJMP __DIVW21U3
__DIVW21U2:
	SBR  R26,1
__DIVW21U3:
	DEC  R25
	BRNE __DIVW21U1
	MOV  R30,R26
	MOV  R31,R27
	MOV  R26,R0
	MOV  R27,R1
	RET

__MODW21U:
	RCALL __DIVW21U
	MOV  R30,R26
	MOV  R31,R27
	RET

;END OF CODE MARKER
__END_OF_CODE:

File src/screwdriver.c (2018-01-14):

/*****************************************************
This program was produced by the
CodeWizardAVR V2.05.3 Standard
Automatic Program Generator
© Copyright 1998-2011 Pavel Haiduc, HP InfoTech s.r.l.
http://www.hpinfotech.com

Project : 
Version : 
Date    : 10.11.2017
Author  : Nikopol
Company : 
Comments: 


Chip type               : ATtiny13A
AVR Core Clock frequency: 9,600000 MHz
Memory model            : Tiny
External RAM size       : 0
Data Stack size         : 16
*****************************************************/
#include <tiny13a.h>
#include <stdlib.h>
#include <delay.h>


#define STATUS_LED_PIN      2
#define STATUS_LED_PORT     PORTB
#define STATUS_LED_ON       STATUS_LED_PORT |= (1<<STATUS_LED_PIN);
#define STATUS_LED_OFF      STATUS_LED_PORT &= ~(1<<STATUS_LED_PIN);
#define STATUS_LED_TOGLE    STATUS_LED_PORT ^= (1<<STATUS_LED_PIN);


#define PWR_PIN             4
#define PWR_PORT            PORTB
#define PWR_OFF             PWR_PORT |= (1<<PWR_PIN);


#define KEY_MODE_VAL        605
#define KEY_FWD_VAL         344
#define KEY_REV_VAL         186
#define KEY_DELTA_VAL       50

#define MODE_FAST           0
#define MODE_MED            1
#define MODE_SLOW           2
#define MODE_COUNT          2

#define TIME_TO_OFF         360 // sec

unsigned char mode = MODE_MED;
unsigned char btn_mode_trig = 0;
unsigned char speed[3] = {0x00, 0x3F, 0x7F};     // speed = 0xFF - need speed;
unsigned int sec, ms, tick; 

// Timer 0 overflow interrupt service routine
interrupt [TIM0_OVF] void timer0_ovf_isr(void)
{
    tick ++;
    if (tick == 5) {
        tick = 0;
        ms ++;
        switch (mode){
            case MODE_FAST:STATUS_LED_ON; break;
            case MODE_MED: if(ms % 200 == 0) {STATUS_LED_TOGLE;} break;
            case MODE_SLOW: if(ms % 500 == 0) {STATUS_LED_TOGLE;} break;
        }
    }
    if (ms >= 1000) {
        sec ++;
        ms = 0;
    } 
    if (sec >= TIME_TO_OFF ){
        PWR_OFF;
    }
}

#define FIRST_ADC_INPUT 3
#define LAST_ADC_INPUT 3
unsigned int adc_data[LAST_ADC_INPUT-FIRST_ADC_INPUT+1];
#define ADC_VREF_TYPE 0x40

// ADC interrupt service routine
// with auto input scanning
interrupt [ADC_INT] void adc_isr(void)
{
static unsigned char input_index=0;
// Read the AD conversion result
adc_data[input_index]=ADCW;
// Select next ADC input
if (++input_index > (LAST_ADC_INPUT-FIRST_ADC_INPUT))
   input_index=0;
ADMUX=(FIRST_ADC_INPUT | (ADC_VREF_TYPE & 0xff))+input_index;
// Delay needed for the stabilization of the ADC input voltage
delay_us(10);
}

// Declare your global variables here

void main(void)
{
// Declare your local variables here

// Crystal Oscillator division factor: 1
#pragma optsize-
CLKPR=0x80;
CLKPR=0x00;
#ifdef _OPTIMIZE_SIZE_
#pragma optsize+
#endif

// Input/Output Ports initialization
// Port B initialization
// Func5=In Func4=Out Func3=In Func2=Out Func1=Out Func0=Out 
// State5=T State4=0 State3=T State2=0 State1=0 State0=0 
PORTB=0x00;
DDRB=0x17;
 
// Timer/Counter 0 initialization
// Clock source: System Clock
// Clock value: 1200,000 kHz
// Mode: Fast PWM top=0xFF
// OC0A output: Inverted PWM
// OC0B output: Inverted PWM
TCCR0A=0xF3;
TCCR0B=0x02;
TCNT0=0x00;
OCR0A=0x00;
OCR0B=0x00;
 
// External Interrupt(s) initialization
// INT0: Off
// Interrupt on any change on pins PCINT0-5: Off
GIMSK=0x00;
MCUCR=0x00;

// Timer/Counter 0 Interrupt(s) initialization
TIMSK0=0x02;

// Analog Comparator initialization
// Analog Comparator: Off
ACSR=0x80;
ADCSRB=0x00;
DIDR0=0x00;

// ADC initialization
// ADC Clock frequency: 600,000 kHz
// ADC Bandgap Voltage Reference: On
// ADC Auto Trigger Source: Timer0 Overflow
// Digital input buffers on ADC0: On, ADC1: On, ADC2: On, ADC3: Off
DIDR0&=0x03;
DIDR0|=0x08;
ADMUX=FIRST_ADC_INPUT | (ADC_VREF_TYPE & 0xff);
ADCSRA=0xAC;
ADCSRB&=0xF8;
ADCSRB|=0x04;

sec = 0;
ms = 0;
tick = 0;
// Global enable interrupts
#asm("sei")

while (1)
      {
        if (abs(adc_data[0] - KEY_MODE_VAL) <=  KEY_DELTA_VAL) {
            if (!btn_mode_trig) {
                // press "mode" key detected
                mode ++;
                if (mode > MODE_COUNT) {
                    mode = 0;
                }
            }
            btn_mode_trig = 1;
        } else {
            btn_mode_trig = 0;
        }
       
        if (abs(adc_data[0] - KEY_FWD_VAL) <=  KEY_DELTA_VAL) {
            //STATUS_LED_OFF;
             OCR0A = speed[mode];
            sec = 0;     
        } else if (abs(adc_data[0] - KEY_REV_VAL) <=  KEY_DELTA_VAL) {
            //STATUS_LED_OFF;
            OCR0B = speed[mode];
            sec = 0;
        } else {
            // off all
            OCR0A=0xFF;
            OCR0B=0xFF;
            //STATUS_LED_OFF;
        }

      }
}

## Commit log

2017-11-11 Commit first version 0.1 of base work code
    [adc_key_val.xlsx]
2017-11-13 Add self power off function. Check litle bugs :)
    [screwdriver.asm, screwdriver.c]
2017-11-16 Add cpu and buttons pcb's
2017-11-17 Check and fix pcb before development
2017-11-18 Fix pcb demensions and components positions
2017-11-20 Add pdf files and schematic
2018-04-02 Add BOM and models files
    [Bateria 18650.ipt, Battery 18650.igs, Battery 18650.ipt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]
